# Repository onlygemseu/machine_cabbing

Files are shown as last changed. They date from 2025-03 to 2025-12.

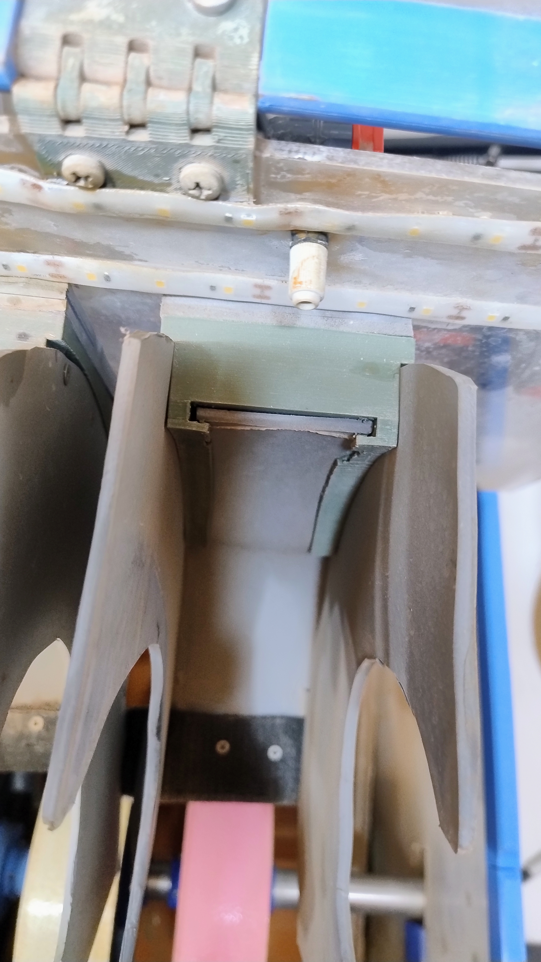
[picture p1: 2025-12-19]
3-Pics/IMG_20251127_175322195_AE.jpg

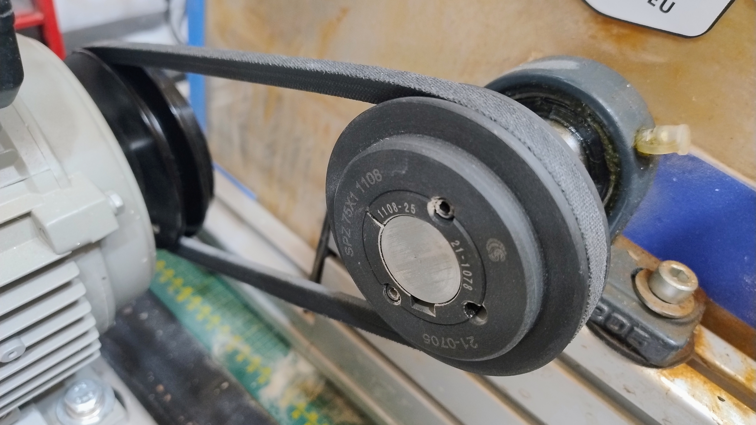
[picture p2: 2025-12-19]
3-Pics/IMG_20251127_174609495_AE.jpg

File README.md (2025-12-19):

# OnlyGems opensource Cabbing machine


## How to use this repo
1. Install windows powertools if you want to see the preview of the printable STL files in your windows folder.
   
2. Install FreeCad in case you want to adjust plexi holders or see the parts assembly in the FCStd files. C4d files are Cinema 4D models made with trial version. 
3. BOM is just as an example. You can switch different wheels, or material vendors. The ones mentioned in BOM are for convenience (available online or via eshops in EU).

## Build instructions (prerequisites)

### DISCLAIMER AND WARNINGS
I am providing this information as my own experience. I hold no responsibility for any possible injuries or financial losses due to any reasons. Electrical wiring, motor connection, lighting should be done by a skilled person or a professional to ensure all wires are properly set up and grounded. IF THE MOTOR IS NOT PROPERLY GROUNDED AND CONNECTED YOU MAY GET ELECTROCUTED EVEN BY TOUCHING A WET WHEEL!!! Be aware that the rotating wheels, shaft, bearings and pulleys have a lot of momentum and can grab your clothing or hair. Always cover the moving parts with proper covers or avoid getting near them or leaning towards them. Especially watch out for the moving belt and pullies!!! Always make sure all parts are tight and wheels, motor, pulley or any other parts are NOT loose. Make sure the tension on the belt is sufficient and it will not slip easily nor be too stiff.
The machine is NOT a toy and if you want your kids to use it, its your own responsibility to look after them and make sure they dont get harmed. 
!!! MACHINE CONSTRUCTION AND USE ARE AT YOUR OWN RISK !!!
1. Ordering the parts 
  
   1.1 When ordering aluminum extrusion profiles, make sure they are of good quality as they hold the structural integrity of your machine. I recommend using T-nuts, because they have a strong grip, once they settle in.

   1.2 The shaft should be made of inox non corrosive steel. This will prevent excesive wear, corosion and sticking of wheel hubs onto the shaft.

   1.3 Make sure the shaft you buy is straight as possible (ideally if available at your local vendor, choose precise inox steel rod). Bent shaft will cause serious vibrations at full speed.

   1.4 Electric motor should be about 0.75kW on 220V with about 1400 rpm. The motor should have a staring and running capacitor (if singlephase) or connected in start/delta setting (3phase motor). In case of 3phase motors you might need a frequency inverter (VFD) to tune your startup power. Star/delta is still not weak enough not to yank your wheels on the startup. Most of the lapidary wheels are designed for upto around 2000 rpm. Overshooting RPM may cause wheel failure and damage the machine or hurt you.

   1.5 In order to prevent excesively fast start and wheel slipage on the shaft, the motor should start progressively. I use a singlephase motor and have changed the startup capacitor to 25 uF (microfarads). These can be bought in any radio/electro shop.

   1.6 You can order pullies with tapper bush. They are really easy to set up on the shafts. I also recommend to choose your pulleys to match the RPM of the motor and desired RPM. [https://www.blocklayer.com/pulley-belt](https://www.blocklayer.com/pulley-belt) (site can be also switched to inches).
   You can buy a single or dual beltpulleys for SPZ belt size.

   1.7 When buying Dome bearings, make sure they come with a lubrication cap as they will accumulate grinding dust and need to be lubricated from time to time. Dome bearings are self-aligning and will have some tolerance when inserting the shaft. Make sure the bearings in the dome do not move freely but significant pressure is needed to roll them out of the dome. Also make sure the shaft goes smootly into the bearing hole. Small rough imperfections on inner bearing hole or shaft can be sanded out, but if the surface is too uneven try a different bearing. (I matched the shaft and the bearing directly in the store)

   1.8 For parts that are exposted to water directly I recommend using inox steel components (bolts and nuts, grub screws). Although not necessary, iit will be easier to disassemble the machine parts when needed.

   1.9 For convenience you can use butterfly nuts in places that you would later frequently disassemble, e.g. front shield hinges.

   1.10 Main water supply hose should be about 1/2" diameter. There are tons of connectivity components to assemble the main line. I used standard gardening hose and connectors with a shutter valve on both sides. The nozzle supply hose is about 4mm in diameter and runs from the splitter to the nozzle. Nozzle sets and splitters are "Gardena microdrip"

   1.11 Nozzles should have either direct or 360° spray area to distribute the water evenly on the wheel surface.

   1.12 Depending on your water source, the best and most flexible is direct connection to water tap using a click-in hose connector. It will allow you to get much higher water pressures on each of your microdrip nozzles. If you have no direct water source at hand, you can use an aquarium pump with a 1/2 hose attachment. I use 1000 l per hour pump. Its okay for work but nozzles tend to clog a bit after accumulating limescale and change the direction of spraying.

   1.13 For 3D printed parts, I used PETG. I dont recommend using PLA. Close to the motor vents, the temperatures might soften the plastic components.   
   
2. Assembly
   
2.1 Frame
   

     2.1.1 Assemble two side frame sections (A,B) by connecting (1) 40160 profile with (2) 20cm 4040 profile with a (11) conneting T8 strip. Secure the connections with (17)grub/setting screws M6x8.

     2.1.2 Connect 2.1.1 to (4) backframe. Slide in M8 T-nuts (12) to secure the (7) 4040 corner brackets on both sides of each 2.1.1 piece. Secure with (15) M8x16 screws. Do not tighten yet, we will adjust the length once we insert the shaft.

     2.1.3 Connect the (3) motor support frame sections to 2.1.2. For the inner angle connection use the (13) inner bracket T8. For the outer connection use a (7) corner bracket. Slide two M8 T nuts onto each of the frame supports. Tack with (15) M8x16 screws. Do not tighten the screws yet.

     2.1.4 Slide in two (12) M8 T nuts into each (1) 40160 profile.

     2.1.5 Place rubber washers over every T nut as in the picture (motor placement, bearings placement).

2.2 Bearings, motor and alignment


     2.2.1 Place A to the far most edge of the (4) backframe and tighten all screws.

     2.2.2 Place B about 90cm far from A.

     2.2.3 Place dome bearings on the top of 40160 profiles and align the T nuts and rubber washers to match the mounting holes of the dome bearing. Do not tighten the bearings yet.

     2.2.4 Loose the setting screws on the bearings and make sure the shaft slides into the mounting hole easily without getting stuck. If it gets stuck at any point, use WD-40 to lubricate the mounting hole and pull out the shaft by wiggling it out. Sand out roughness that made the shaft stuck and repeat trying until the shaft gets into the mounting hole without catching on the mounting hole.

     2.2.5 Roughly align the bearings and insert the shaft across the bearings from A to B. Make sure the bearings are "somewhere in the middle" of the 40160 profile and handtighten them. Place the pulley of your choice on the driving end of your shaft and secure it against movement.

     2.2.6 adjust the B so that you would get enough space for your wheels. Max with this sizing is 8 wheels with 50mm width and 200mm diameter. The spacing in between the wheels is roughly 3-4cm. The far end of the shaft on the A side in the bearing should not exceed the bearing mounting hole length.

     2.2.7 If you are Ok with your A-B alignment secure all the (7) corner brackets by tightning the screws.

     2.2.8 Install the drive pulley on your electric motor shaft and align the (3) motor mounting supports to match the mounting holes on the motor. Place the drive belt on both pulleys and adjust the motor assembly placement util the belt is driven straight with no sideways deviation.

     2.2.9 Remove the motor and the shaft from the bearings and tighten all inner and outer corner brackets on the (3) motor supports.

  2.3 Assembling wheels on the shaft

     2.3.1 Based on your wheel hubs and you wheel setup, print the respective hub brackets or design your own based on the wheels used.

     2.3.2 Tighten the pulley on the shaft. You will be inserting the wheels from the other end (side A). Insert the shaft into the bearing and leave 10-15cm on the pulley side (B). Tighten the bearing on side B and firmy rotate the bearing out of its dome by pulling the shaft on side A outwards. This will allow you to insert wheels on the shaft.

     2.3.3 Split the shaft with a marker for placement of your wheels. They should be roughly 4cm from each other. Slide in your printed hub brackets accordingly on both sides of the wheels and secure them with settings screws. Push the shaft back so that the dome bearing on side B will get back to its original position and slide the shaft into the bearing on side A.

     2.3.4 Make sure the bearings are roughly in the same position on both (1) 40160 profiles. Tighten the screws on both bearings and try to rotate the whole shaft assembly by hand. The shaft should move smoothly, and based on your wheel setup, should have some momentum when slowing down. Check if the wheels are not wobbling or moving sideways on the shaft. If your plastic hub brackets are not gripping to the wheel hubs enough, you can spray them with rubber spray and let dry out for a few hours. This will enhance the hub bracket grip and will better distribute the momentum on start.

2.4 Motor and drivetrain

     2.4.1 Place the motor on the motor support profiles. Install the drive belt on the pulleys and tighten it by pushing the motor farther from the wheel shaft. The drive belt should not be slipping easily but also should not be too tight. Align the angle of your motor with the wheel shaft so that the belt will be running smoothly without grabbing the pulley edges. This might cause heat buildup and excesive wear and/or the belt might snap more easily. Make sure to cover the belt and pulleys when the machine is operational to prevent any injury.

     2.4.2 Based on the motor you are using, the start of the motor should be slower and smooth. If the motor yanks the wheel shaft, your wheels will likely slip or can grind into the shaft and you wont be able to slide them out later. In my case im using 0.75kW single phase motor. I changed the starting capacitor to 25uF (microfarads), which is still a bit to strong for the start but definitely better than the original 250uF. Make sure the motor rotation is correct. If not switch it based on the motor installation diagram of your motor. The wheels should be rotating downwards/to you when you are in front of them. Do not change the running capacitor - this might cause excesive heat buildup, motor failure or capacitor can sweal and blow up. If you are using 3 phase motor, use the star/delta setting for startup and running. In 3phase your startup will most likely be still too powerful so you will need a frequency inverter (VFD) to tune your motor startup. VFD is an expensive component, so thats why Im sticking with single phase motor and a smaller capacitor.
   IF YOU ARE NOT FAMILIAR AND CONFIDENT WITH SETTING UP YOUR ELECTRICAL WIRING, MAKE SURE TO CONTACT A PROFESSIONAL TO SET IT UP FOR YOU. MISTAKES IN THIS STEP CAN CAUSE YOU INJURIES, DESTROY YOUR MOTOR OR IN EXTREME CASES CAUSE FIRE.   

     2.4.3 Secure all bolts and screws on bearings, frame, motor and bearing settings screws holding the shaft. Tighten the tapper bush screws.

     2.4.4 When testing the motor, DOUBLE CHECK THAT ALL THE SCREWS ARE TIGHT on the frame and motor and bearing mounts. First, step aside from the wheel assembly and only then start the motor. Do a really short run first (split of a second) to see if nothing starts resonating or if the wheels are not getting yanked with too much power (squeeking noises). If they do, either adjust the motor power on startup or tighten the lose hub brackets on your wheels. If you observe vibrations, try to wiggle the wheels sideways. If they move tighten them to hold their place on the shaft.

     2.4.5 Do a second test run now reaching the full speed. Observe any heavy resonation, wheel wobbling, belt slippage and other noises. In case the soft wheels are wobbling or resonating, you will not be able to do anything with them unless you return these wheels to your reseller. In case your aluminum hub wheels are vibrating, its possible that they werent correctly aligned when manufactured. It is also possible that your shaft is bent or bearings are not correctly adjusted. Before returning your wheels to the reseller, make sure the problem is not on your side. First try to run the shaft without wheels to see if it is vibrating. If it is, let a professional straighten shaft and align the bearings again.

 2.5 Wheel covers and plexi (TBD)

 2.6 Lighting (TBD)

 2.7 Water lines (TBD)

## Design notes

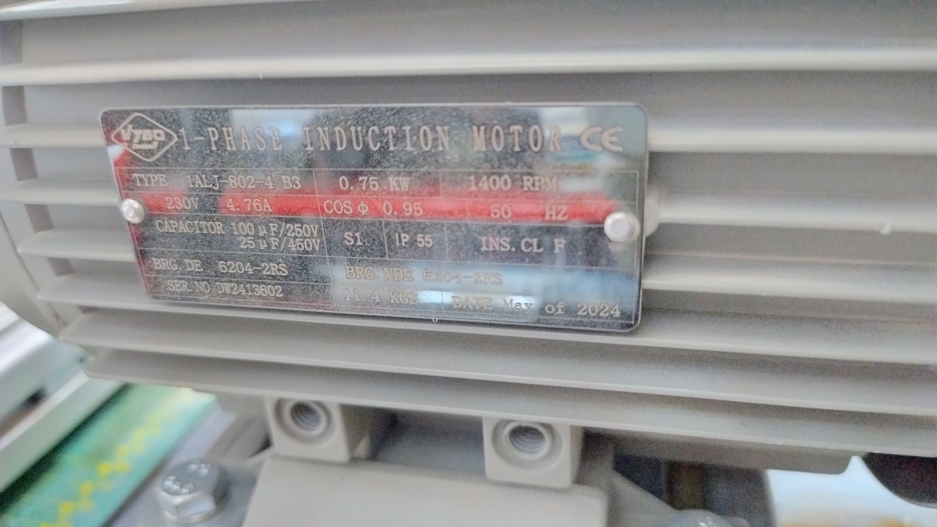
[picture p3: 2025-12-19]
3-Pics/IMG_20251127_175921280_HDR_AE.jpg

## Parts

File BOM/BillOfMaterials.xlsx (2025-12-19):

No | Part | PartName | Part desc | Pcs | Price per Pcs | Total price | Shop | Pozn. | Url
1 | Frame | Aluminum slot profile 40160 | 20cm length | 2 | 11.38 | 22.76 | AluxProfile | For bearings | https://www.aluxprofile.com/aluminium-slot-profile-40160/a3838
2 | Frame | Aluminum slot profile 4040 | 20cm length | 2 | 3.94 | 7.88 | AluxProfile | side frame | https://www.aluxprofile.com/aluminium-slot-profile-4040/a3619
3 | Frame | Aluminum slot profile 4040 | 30cm length | 2 | 5.9 | 11.8 | AluxProfile | motor stand | https://www.aluxprofile.com/aluminium-slot-profile-4040/a3619
4 | Frame | Aluminum slot profile 4040 | 120cm length | 1 | 23.6 | 23.6 | AluxProfile | back frame | https://www.aluxprofile.com/aluminium-slot-profile-4040/a3619
5 | Frame | Cover cap 40160 |  | 2 | 1.83 | 3.66 | AluxProfile |  | https://www.aluxprofile.com/cover-cap-40160/a3843
6 | Frame | Cover cap 4040 |  | 4 | 0.3 | 1.2 | AluxProfile |  | https://www.aluxprofile.com/cover-cap-4040/a3528
7 | Frame | Corner bracket 4040 |  | 6 | 0.92 | 5.52 | AluxProfile |  | https://www.aluxprofile.com/corner-bracket-4040/a3818
8 | Frame | Rubber foot |  | 14 | 0.97 | 13.58 | AluxProfile |  | https://www.aluxprofile.com/rubber-foot/a3746
9 | Frame | M5x12 screw | ISO 7380 M5x12 | 14 | 0.09 | 1.26 | AluxProfile | for feet | https://www.aluxprofile.com/hexagon-socket-button-head-screw-iso-7380-m5x12/a3819
10 | Frame | Roll-in T slot nut, 40-series M5 | 8-4-M5.40 | 14 | 0.27 | 3.78 | AluxProfile | for feet | https://www.aluxprofile.com/roll-in-t-slot-nut-40-series-m5/a3677
11 | Frame | Connecting strip T8 | 8-9 | 4 | 3.31 | 13.24 | AluxProfile | side frame | https://www.aluxprofile.com/connecting-strip-t8/a3625
12 | Frame | Slide-in T-slot nut, T slot 8 M8 | 8-3-M8 | 20 | 0.32 | 6.4 | AluxProfile | motor, corners | https://www.aluxprofile.com/slide-in-t-slot-nut-t-slot-8-m8/a3607 | plexi | 75x28x3,5 | vrch
13 | Frame | Inner bracket T8 | 8-6 | 2 | 1.59 | 3.18 | AluxProfile | motor stand | https://www.aluxprofile.com/inner-bracket-t8/a3682 |  | 72,5x37 | zadna stena
14 | Frame | Hex socket head cap screw M8 x 40 | ISO 4762-M8x40 | 4 | 0.3 | 1.2 | AluxProfile | bearings | https://www.aluxprofile.com/hexagon-socket-head-cap-screw-iso-4762-m8x40/a3824?search=ISO%204762-m8x40 |  | 42x32,5 X2 | boky
15 | Frame | Hex socket buttonhead screw M8 x 16 | ISO 7380 M8x16 | 16 | 0.16 | 2.56 | AluxProfile | corners | https://www.aluxprofile.com/hexagon-socket-button-head-screw-iso-7380-m8x16/a3823?filter=15%2C24 |  | 72,5x13,5 | celny kryt
16 | Frame | Washer M8 | ISO 7093 M8 | 26 | 0.06 | 1.56 | AluxProfile |  | https://www.aluxprofile.com/washer-iso-7093-m8/a3657
17 | Frame | Setting screw M6x8 | DIN 914 M6x8 | 16 | 0.06 | 0.96 | AluxProfile | connecting strips | https://www.aluxprofile.com/setting-screw-din-914-m6x8/a3743
18 | Cover | Plexi glass 4mm thick 150x50cm | Gutta Plexisklo Hobbyglass transparent | 1 | 26.99 | 26.99 | OBI | 2x side, face, back | https://www.obi.sk/plastove-stresne-krytiny/gutta-plexisklo-hobbyglass-transparentne-1500-x-500-x-4-mm/p/4246971
19 | Cover | Plexi glass 4mm thick 100x50cm | Gutta Plexisklo Hobbyglass transparent | 1 | 19.99 | 19.99 | OBI | top cover | https://www.obi.sk/plastove-stresne-krytiny/gutta-plexisklo-hobbyglass-transparentne-1000-x-500-x-4-mm/p/4246807
20 | Shaft | Inox full rod 25mm | I-3000 AlSi 304 90cm length | 1 | 20 | 20 | Elektra reklama | shaft | https://www.hliniknerez.sk/tovar/2256/nerezova-gulatina
21 | Bearing | Dome bearing UCP205 |  | 2 | 5.17 | 10.34 | PO Bearings |  | https://www.loziska-bearings.sk/e-shop/action/productdetail/oc/29/product/lozisko-ucp205-standard-q.xhtml
22 | Drive | Pulley | SPZ 75x1 1108 | 1 | 10.53 | 10.53 | PO Bearings |  | https://www.loziska-bearings.sk/e-shop/remenica-spz-75-1-tb-1108-optibelt/p-4256078.xhtml
23 | Drive | Pulley | SPZ 85x1 1210 | 1 |  | 0 | PO Bearings |  | https://www.loziska-bearings.sk/e-shop/remenica-spz-85-1-tb-1210-optibelt/p-4256082.xhtml
24 | Drive | Tapper bush | 1108-25 | 1 | 3.96 | 3.96 | Tyma |  | https://www.tyma.cz/produkty/tb-1108-25/
25 | Drive | Tapper bush | 1210-19 | 1 | 4.92 | 4.92 | Tyma |  | https://www.tyma.cz/produkty/tb-1210-19/
26 | Drive | Drive belt | SPZ 637 Lw 650 La | 1 | 1.45 | 1.45 | PO Bearings |  | https://www.loziska-bearings.sk/e-shop/remen-97-637lw-650la-spz/p-5359516.xhtml
27 | Drive | Motor | Single phase 230V 0,75kW 1ALJ802-4 | 1 | 152.41 | 152.41 | Vybo electric |  | https://vyboelectric.sk/obchod/jednofazovy-elektromotor-230v-075kw-1alj802-4/
28 | Drive | Startup capacitor | 25uF 450V | 1 | 5.95 | 5.95 | RV elektronik |  | https://www.rv-elektronik.eu/rv-elektronik/eshop/7-1-Kondenzatory/18-2-rozbehove/5/2340-Rozbehovy-kondenzator-25uF
29 | Misc | 3D printer filament | PETG | 2 | 15.28 | 30.56 | Datacomp |  | https://datacomp.sk/c-tech-premium-line-tlacova-struna-filament-petg-1-75mm-nebeska-modra_d483825.html
30 | Misc | Screws, settings screws, small bolts | package of mix | 2 | 20 | 40 | Mall.sk ??
31 | Cooling | Hex bolt M6x60 |  | 32 | 0.1 | 3.2 | OBI | M6x60 / M6x80 | https://www.obi.sk/strojne-skrutky/lux-strojna-skrutka-m6-x-60-mm-pozinkovana-uplny-zavit-100-kusov/p/3860871
32 | Cooling | Hex nut M6 | 100 pcs package | 1 | 2.39 | 2.39 |  | 64pcs min - holder | https://www.obi.sk/sesthranne-matice/lux-sesthranna-matica-m6-pozinkovana-100-kusov/p/3860400
33 | Cooling | PZ screw for wood 3,5x16mm | 200 pcs package | 1 | 3.39 | 3.39 |  | 200pcs wheel covers | https://www.obi.sk/univerzalne-a-drevotrieskove-skrutky/lux-skrutka-so-zapust-hlavou-pz-plny-zavit-zlto-pozinkovany-200-ks-3-5-x-16-mm/p/3939915
34 | Cooling | Water pump | Tetra WP1000 1000l/h | 1 | 26.8 | 26.8 | Mall.sk |  | https://www.mall.sk/akvaristika/tetra-cerpadlo-wp-1000-1000l-h-100098177208
35 | Cooling | Hose | 1/2" hose 2m | 2 | 2.59 | 5.18 | OBI |  | https://www.obi.sk/zahradne-hadice/gardena-hadica-flex-13-mm-1-2-metraz/p/4634721
36 | Cooling | Nozzle hose | 4mm hose 2m | 2 | 0.99 | 1.98 | OBI |  | https://www.obi.sk/zahradne-hadice/fitt-akvaristicka-hadica-zelena-15-bar-pr-4-mm-metraz/p/2229250
37 | Cooling | Hose T reduction 5 pcs pack | 10pcs = 2 pack 8333-20 | 2 | 4.29 | 8.58 | OBI |  | https://www.obi.sk/zavlazovaci-system-micro-drip/gardena-redukcny-t-kus-13-mm-1-2-4-6-mm-3-16-/p/3077989
38 | Cooling | Nozzle hose valve 5pcs pack | 10pcs | 2 | 7.49 | 14.98 | OBI |  | https://www.obi.sk/zavlazovaci-system-micro-drip/gardena-regulacny-ventil-micro-drip-pr-4-6-mm-3-16-5-ks/p/2034098
39 | Cooling | Nozzle 5pcs pack | 10pcs | 2 | 2.89 | 5.78 | OBI |  | https://www.obi.sk/zavlazovaci-system-micro-drip/gardena-hmlova-tryska/p/1976133
40 | Cooling | Hose fast clamp | 1/2" 4pcs | 4 | 5.09 | 20.36 | OBI |  | https://www.obi.sk/pripojky-a-spojky/gardena-rychlospojka-13-mm-1-2-15-mm-5-8-/p/4797650
41 | Cooling | Hose fast clamp with valve | 1/2" 2pcs | 2 | 9.19 | 18.38 | OBI |  | https://www.obi.sk/pripojky-a-spojky/gardena-regulacny-ventil/p/9401605
42 | Cooling | Hose joint | 1/2" 2pcs | 2 | 0.99 | 1.98 | OBI |  | https://www.obi.sk/pripojky-a-spojky/hadicova-spojka/p/2229128
43 | Power | Power cable | Flex H07RN-F 3G4 3m | 3 | 3.2987 | 9.8961 | Hagard hal |  | https://www.hagard.sk/produkty/kabel-ohybny-h07rn-f-3g4-guma-cierny
44 | Power | Switchbox | Switching box 85x85x40 | 1 | 1.7434 | 1.7434 | Hagard hal |  | https://www.hagard.sk/produkty/krabica-rozbocovacia-2000342-a-11-85x85x40mm-bez-vyvodiek-siva
45 | Power | power switch | 2 position 250v / 15A Red or green | 2 | 0.77 | 1.54 | CB elektro |  | https://www.cbelektro.sk/vypinac-koliskovy-on-off-2pol-250v-15a-cerveny-hdx-p40463?gad_source=1
46 | Power | power plug | 250v 16A 2p | 1 | 2.524 | 2.524 | Hagard hal |  | https://www.hagard.sk/produkty/vidlica-5536-2154-250v-16a-3p-pvc-biela
47 | Power | Wago clamp | 3 pole 0,2-4mm2 10 pcs | 10 | 0.5796 | 5.796 | Hagard hal |  | https://www.hagard.sk/produkty/svorka-krabicova-221-413-3x0-2-4-0mm2-3-polova-wago
48 | Wheels | Sintered wheel 100grit | 50mm x 200mm x 25mm bore | 1 | 468 | 468 | Baltic abrasives
49 | Wheels | Sintered wheel 220grit | 25mm x 200mm x 25mm bore | 1 | 340 | 340 | Baltic abrasives
50 | Wheels | Electroplated hard wheel 400 grit | 50mm x 200mm x 25,4mm bore | 1 | 120 | 120 | Dimapa
51 | Wheels | Soft Premium REZ wheel 600 grit | 50mm x 200mm x 25,4mm bore | 1 | 84.95 | 84.95 | Baltic abrasives
52 | Wheels | Soft Premium REZ wheel 1200 grit | 50mm x 200mm x 25,4mm bore | 1 | 84.95 | 84.95 | Baltic abrasives
53 | Wheels | Soft Premium REZ wheel 3000 grit | 50mm x 200mm x 25,4mm bore | 1 | 84.95 | 84.95 | Baltic abrasives
 |  |  |  |  | Total | 1768.5895
 |  |  |  |  | Withotu wheels | 585.7395

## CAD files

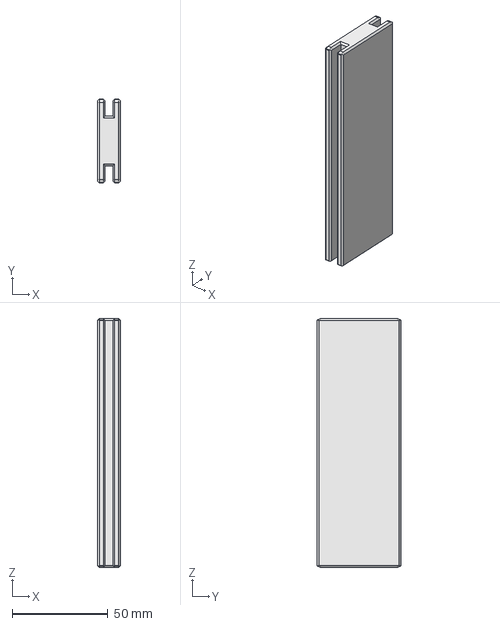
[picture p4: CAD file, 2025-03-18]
1-Printables/1-1-MachineParts/6-0-drziakNaPlexi.FCStd
12.0 x 44.0 x 130.0 mm

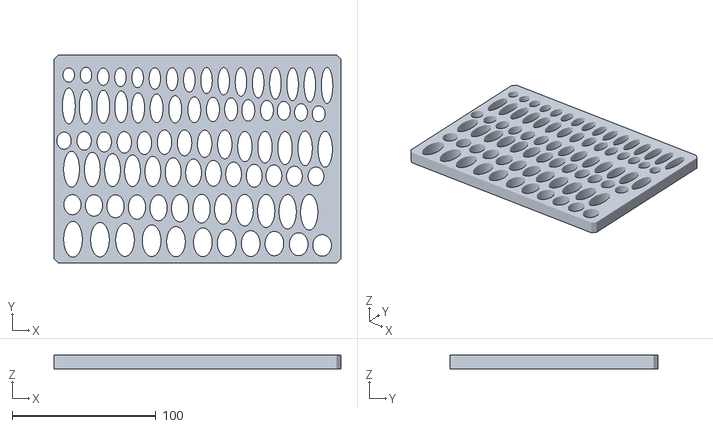
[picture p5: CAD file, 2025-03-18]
1-Printables/1-2-Stencils/Oval_10x8-25x13.stl
200.0 x 145.0 x 10.0

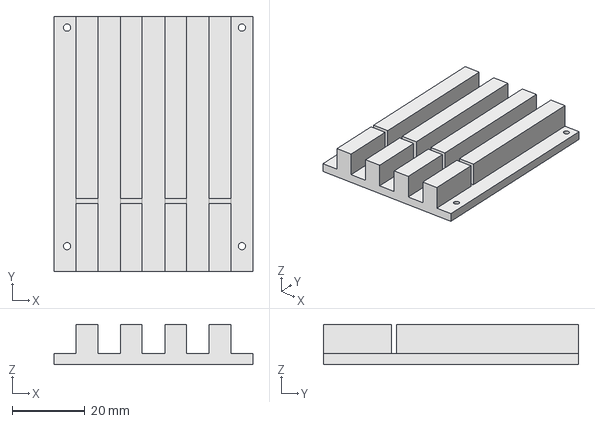
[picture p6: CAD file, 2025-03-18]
1-Printables/1-3-DopCutters/rezackaNaDopsticky6mm.FCStd
54.6 x 70.0 x 11.0 mm

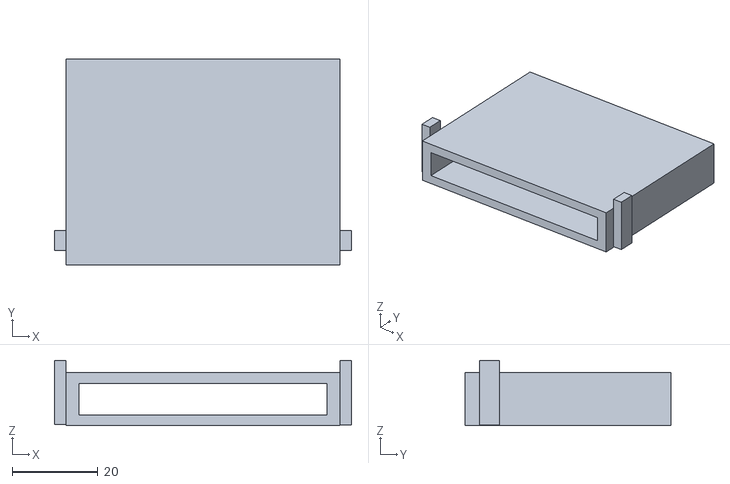
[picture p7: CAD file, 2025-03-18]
1-Printables/1-4-Misc/LightHolder-Body.stl
69.4 x 48.0 x 15.2

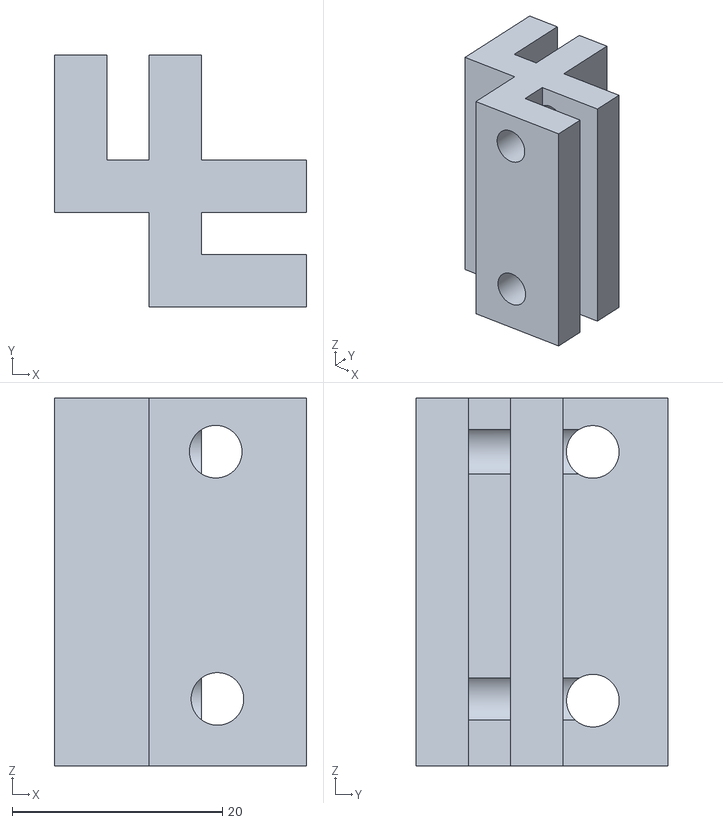
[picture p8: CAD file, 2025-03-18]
1-Printables/1-1-MachineParts/7-3-ostryRohPlexi-h.stl
24.0 x 24.0 x 35.0

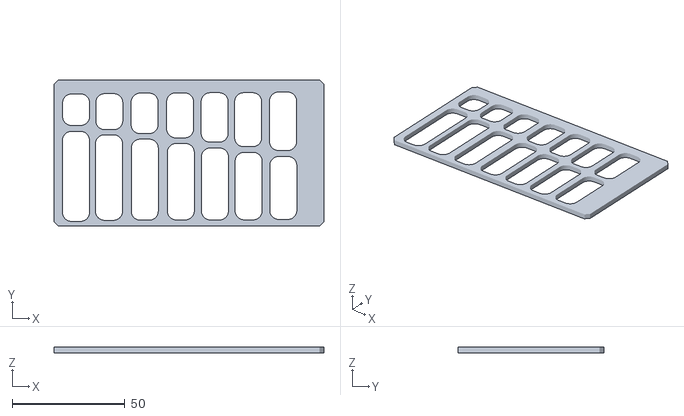
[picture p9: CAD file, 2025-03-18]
1-Printables/1-2-Stencils/rect_4Fillet_12x13-12x40.stl
120.0 x 65.0 x 2.50

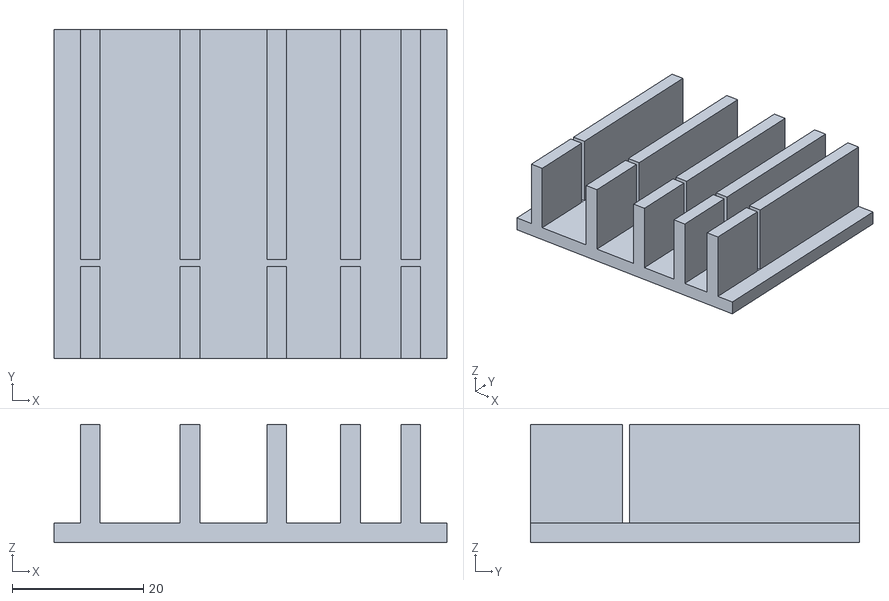
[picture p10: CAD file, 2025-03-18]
1-Printables/1-3-DopCutters/rezackaNaDopsticky-Body.stl
59.8 x 50.0 x 18.0

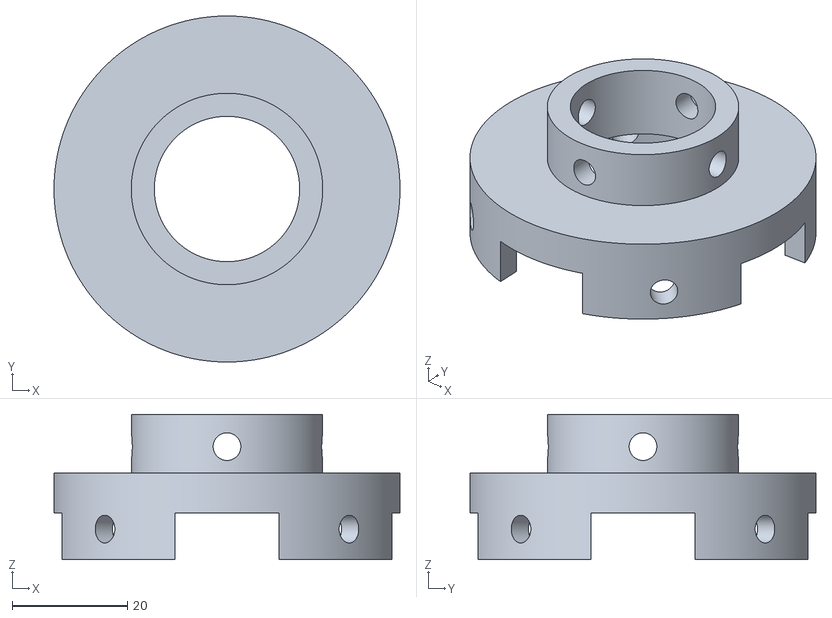
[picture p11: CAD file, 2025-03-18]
1-Printables/1-1-MachineParts/3-1-20cmKotucRedukcia25-Ozubena-Enh-PremiumRez51mm.stl
60.0 x 60.0 x 25.2

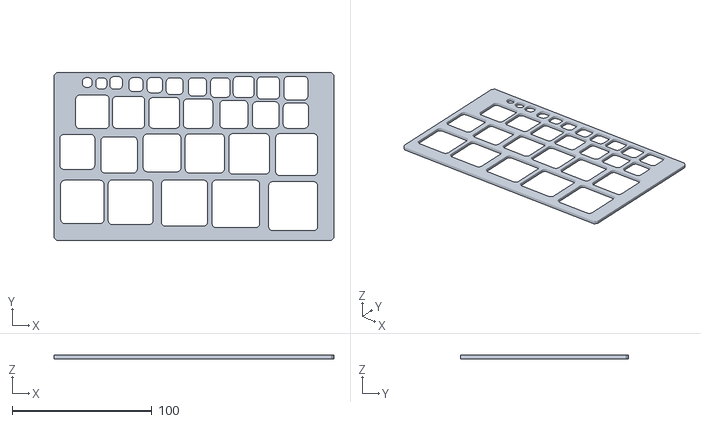
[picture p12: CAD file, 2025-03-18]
1-Printables/1-2-Stencils/cabTemp_Square3_7-35.stl
200.0 x 120.0 x 2.50

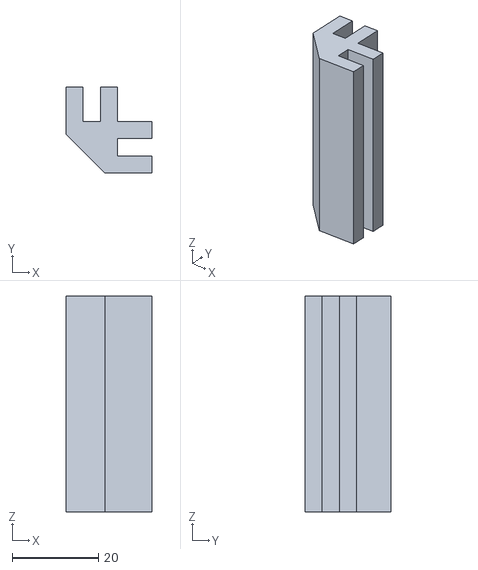
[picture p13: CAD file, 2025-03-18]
1-Printables/1-1-MachineParts/7-4-plexiSpojkaDlha.stl
20.0 x 20.0 x 50.0

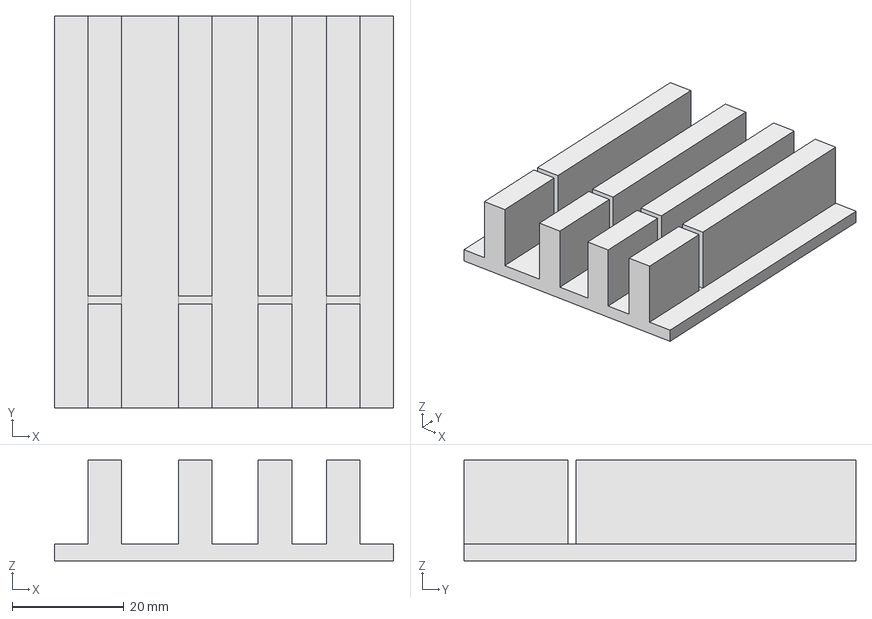
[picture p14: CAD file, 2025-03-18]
1-Printables/1-3-DopCutters/rezackaNaDopsticky2.FCStd
60.6 x 70.0 x 18.0 mm

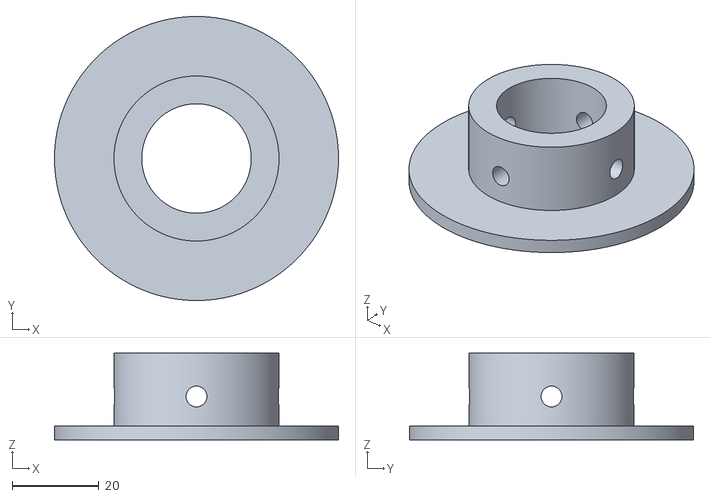
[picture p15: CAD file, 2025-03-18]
1-Printables/1-1-MachineParts/4-1-HardWheel-20cm-2KotucRedukcia25-jemnaSCervikmi.stl
65.4 x 65.4 x 20.0

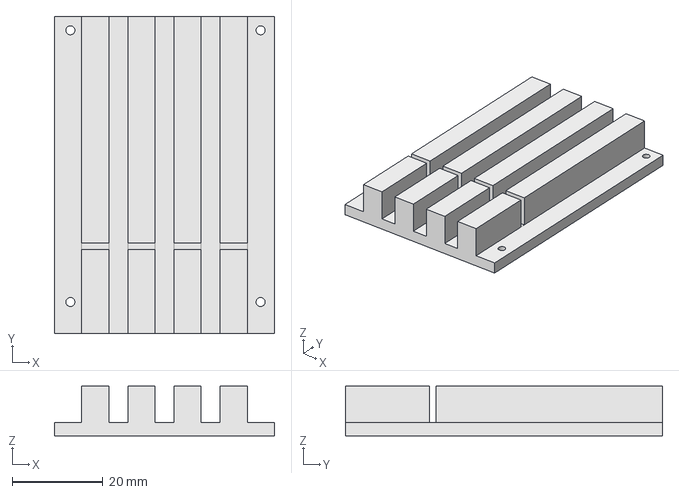
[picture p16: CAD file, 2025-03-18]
1-Printables/1-3-DopCutters/rezackaNaDopsticky4mm.FCStd
48.6 x 70.0 x 11.0 mm

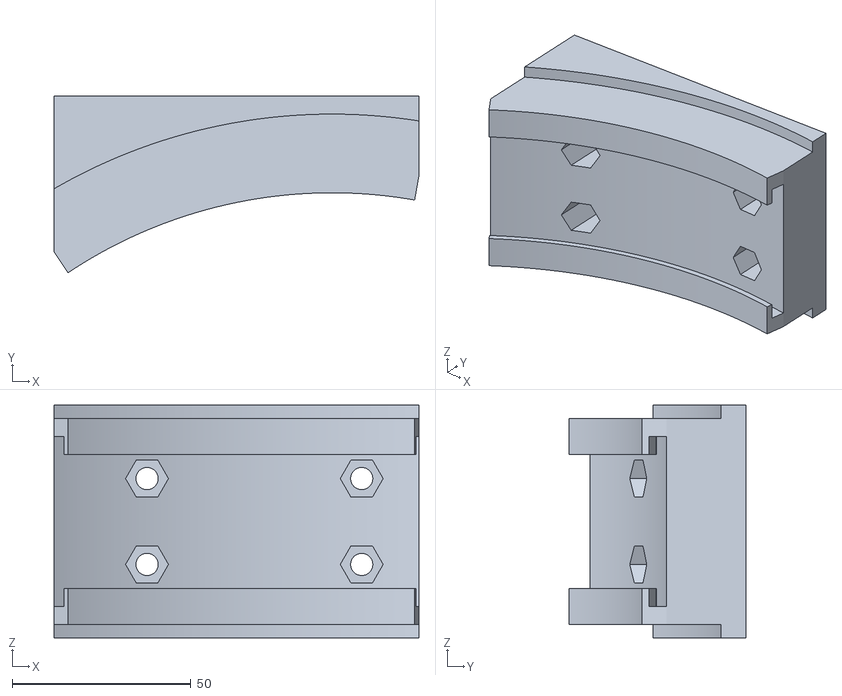
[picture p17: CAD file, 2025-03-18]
1-Printables/1-1-MachineParts/1-1-drziakNaKrytyKotuca.stl
102.0 x 49.4 x 65.0

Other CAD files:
1-Printables/1-4-Misc/LightHolder.FCStd
1-Printables/1-3-DopCutters/rezackaNaDopsticky.FCStd
1-Printables/1-2-Stencils/rect_4Fillet_12x13-12x36.stl
1-Printables/1-2-Stencils/cabTemp_Square2_5-35.stl
1-Printables/1-1-MachineParts/1-2-drziakNaTrysku.stl
1-Printables/1-1-MachineParts/4-2-CabstonSoft-Hardwheel-20cmKotucRedukcia25.stl
1-Printables/1-1-MachineParts/5-1-Glass_to_glass_hinge.stl
1-Printables/1-1-MachineParts/6-1-priama_obojstranna.stl
1-Printables/1-1-MachineParts/6-2-priama_zahybova.stl
1-Printables/1-1-MachineParts/7-1-damper_poklop.stl
1-Printables/1-1-MachineParts/7-2-ostryRohPlexi.stl
1-Printables/1-2-Stencils/cabRD_100°_20-50_3_1_4,5,6.stl
1-Printables/1-2-Stencils/cabTemp_Oval4-35.stl
1-Printables/1-2-Stencils/cabTemp_OvalPill.stl
1-Printables/1-2-Stencils/cabTemp_Square4_9-35.stl
1-Printables/1-2-Stencils/cabTemp_Square5_11-35.stl
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

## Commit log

2025-03-18 Added printables for cabbing machine
    [1-1-drziakNaKrytyKotuca.stl, 1-2-drziakNaTrysku.stl, 3-1-20cmKotucRedukcia25-Ozubena-Enh-PremiumRez51mm.stl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]
2025-11-27 Added BOM
    [BillOfMaterials.xlsx]
2025-11-27 Added frame FreeCad model v1
2025-11-27 Update README.md
    Added assembly sections and basic information
2025-12-19 added pics of built machine
    [BillOfMaterials.xlsx]
